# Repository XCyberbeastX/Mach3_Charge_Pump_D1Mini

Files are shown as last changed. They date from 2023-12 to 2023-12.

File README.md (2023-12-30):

# Mach3_Charge_Pump_D1Mini(ESP8266)

## Note:
This project is based on this [YouTube video](https://www.youtube.com/watch?v=voYk2AVyjqQ). Please be aware that I am not a professional circuit board designer and this information is shared from a hobbyist's perspective. Implementing this project is at your own risk, and it's advised to consult with a professional if needed.

## Info:
The charge pump circuit prevents the spindle from unintentionally starting while not using Mach3 with a parallel port. Especially during power up or down of the pc, this can lead to the parallel port outputs being switched randomly, posing a safety risk. The circuit, reads the 25/12,5 Khz signal of Mach3 and enables/disables the machine via a relay.

The Webinterface of the D1Mini (ESP8266) provides a easy way to read the charge pump frequency and relay state and can be further extended as needed.

The D1 Mini can be flashed using OTA through the 'ip/update' page after the first inital flash.

## 

*Make sure to enable the charge pump feature in Mach3 and assign a free pin.*

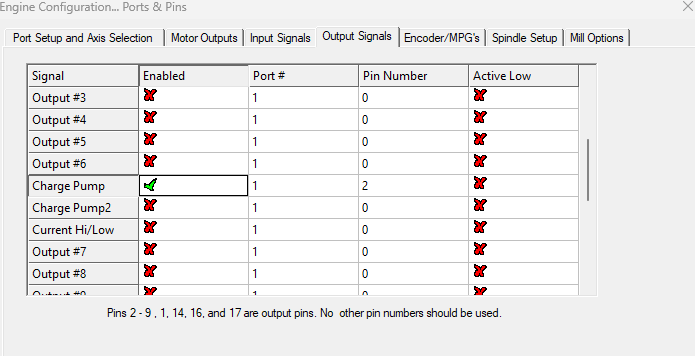
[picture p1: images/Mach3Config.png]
Mach3 Config


## Screenshots

*Website image*

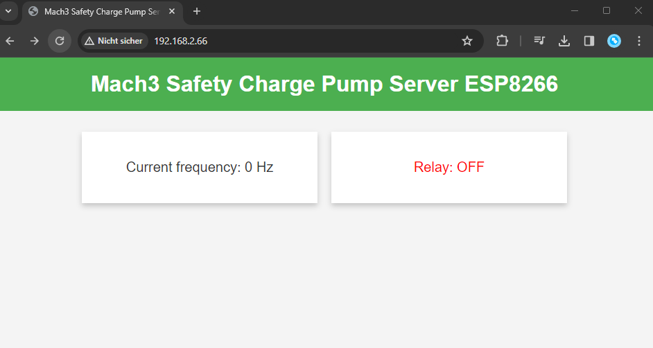
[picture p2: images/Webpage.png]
Webpage


*finished PCB for THT-Soldering, with bigger pads*

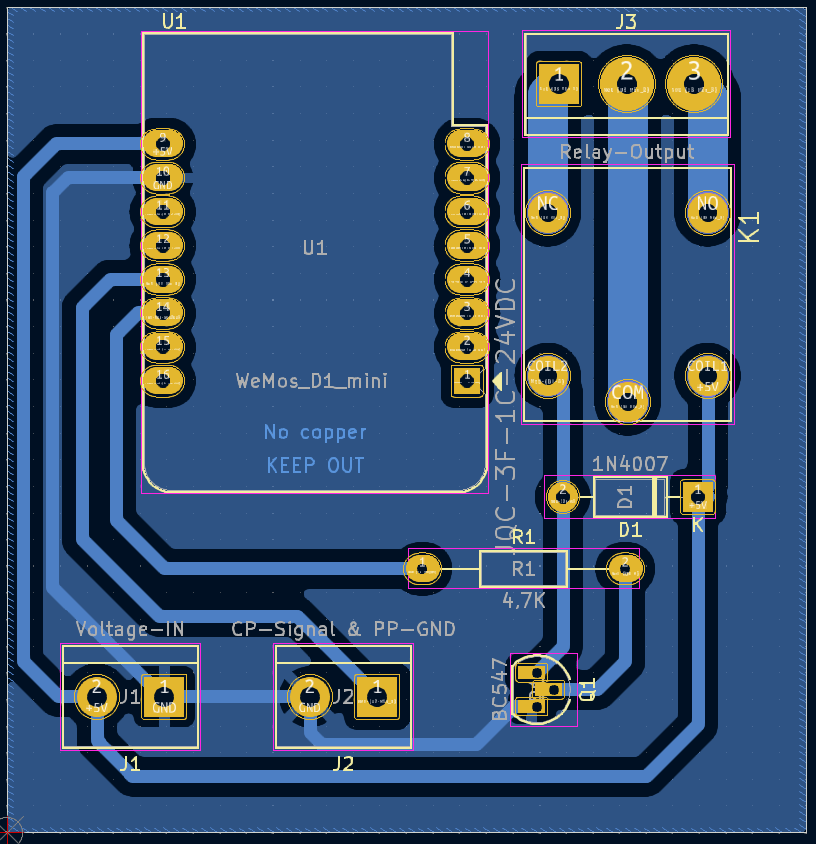
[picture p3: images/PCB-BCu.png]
PCB


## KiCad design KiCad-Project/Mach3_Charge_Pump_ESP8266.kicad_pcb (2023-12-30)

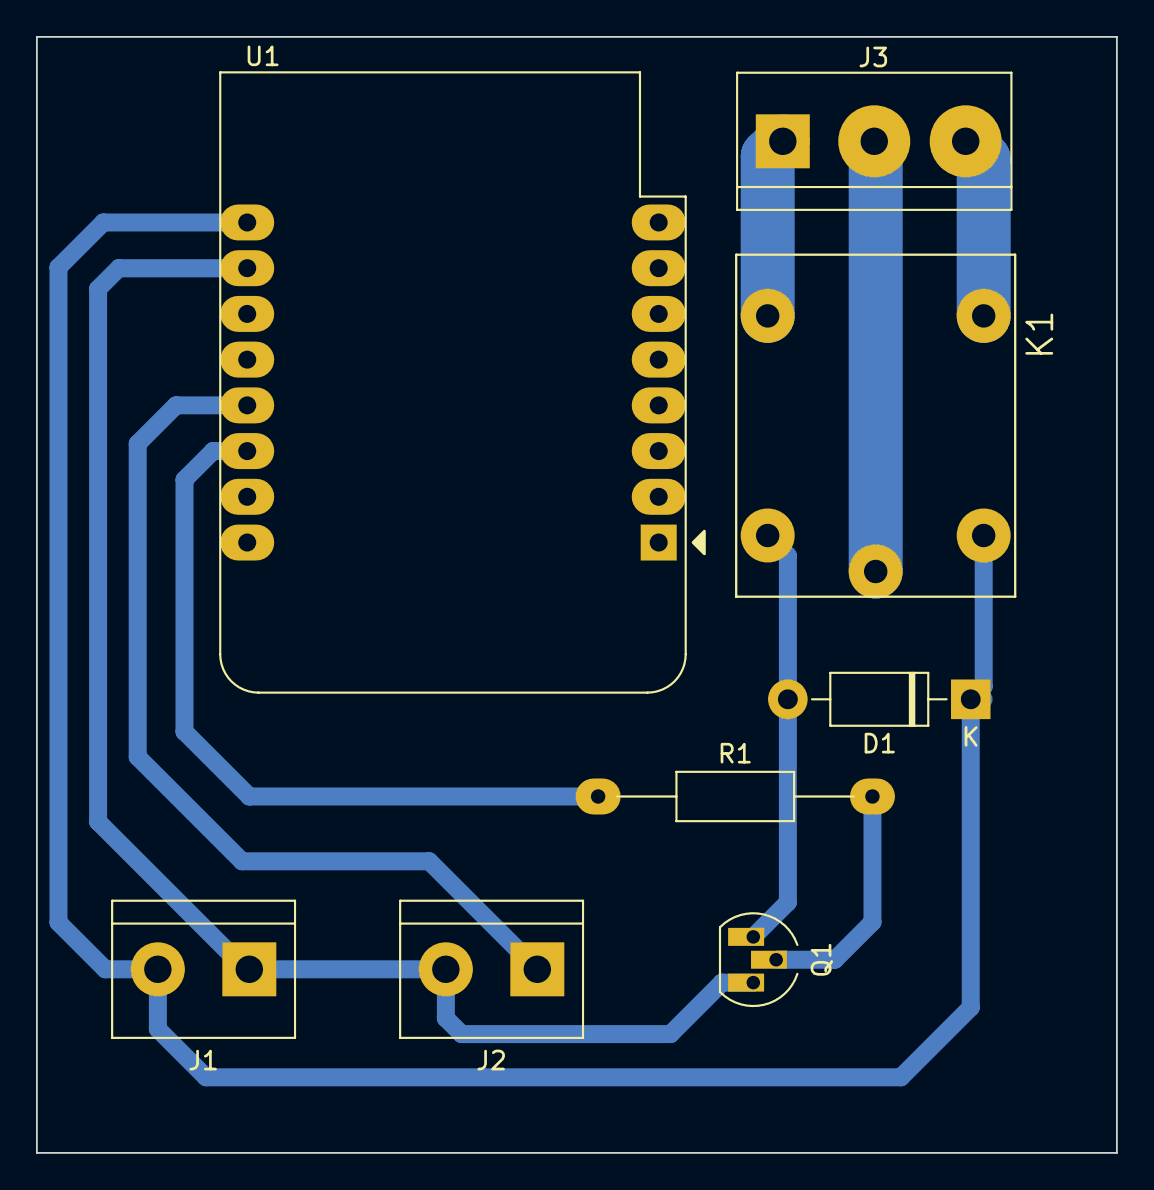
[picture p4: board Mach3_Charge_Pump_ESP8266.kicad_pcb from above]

Board: 2 copper layers, 60.0 x 62.0 mm, 8 parts (0 on the bottom side), 9 nets.

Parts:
D1: 1N4007; D_DO-41_SOD81_P10.16mm_Horizontal
J1: Voltage-IN; TerminalBlock_bornier-2_P5.08mm
J2: CP-Signal & PP-GND; TerminalBlock_bornier-2_P5.08mm
J3: Relay-Output; TerminalBlock_bornier-3_P5.08mm
K1: JQC-3F-1C-24VDC; RELAY_JQC-3F-1C-24VDC
Q1: BC547; TO-92L_HandSolder
R1: 4,7K; R_Axial_DIN0207_L6.3mm_D2.5mm_P15.24mm_Horizontal
U1: WeMos_D1_mini; WEMOS_D1_mini_light

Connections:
+5V: D1.1 (K), J1.2, K1.COIL1, U1.9 (5V)
GND: J1.1, J2.2, Q1.3 (E), U1.10 (GND)
unnamed: D1.2 (A), K1.COIL2, Q1.1 (C)
unnamed: J2.1, U1.13 (SDA/D2)
unnamed: J3.1, K1.NC
unnamed: J3.2, K1.COM
unnamed: J3.3, K1.NO
unnamed: Q1.2 (B), R1.2
unnamed: R1.1, U1.14 (SCL/D1)

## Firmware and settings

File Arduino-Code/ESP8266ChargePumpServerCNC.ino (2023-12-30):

#include <ESP8266WiFi.h>
#include <ESPAsyncTCP.h>
#include <ESPAsyncWebServer.h>
#include <AsyncElegantOTA.h>

enum RelayState
{
  ON,
  OFF
};

AsyncWebServer server(80);
const char *ssid = "CHANGE ME";
const char *password = "CHANGE ME";

// Change values according to your needs.
const byte MEASURE_PIN = 4;
const byte RELAY_PIN = 5;
const int THRESHOLD_FREQ = 25000;
const int MAX_DEVIATION = 5000;
const int MIN_REPS = 2;
const int TIMEOUT = 250;

RelayState currentRelayState = RelayState::OFF;
int reps = 0;
long currentFreq = 0;

void setup()
{
  Serial.begin(115200);
  WiFi.begin(ssid, password);

  pinMode(MEASURE_PIN, INPUT);
  pinMode(RELAY_PIN, OUTPUT);
  // Change the relay state according to your needs.
  digitalWrite(RELAY_PIN, LOW);
  currentRelayState = RelayState::OFF;

  while (WiFi.status() != WL_CONNECTED)
  {
    delay(500);
    Serial.print(".");
  }

  Serial.println("");
  Serial.print("Connected with SSID: ");
  Serial.println(ssid);
  Serial.print("Device ip-address: ");
  Serial.println(WiFi.localIP());

  server.on("/", HTTP_GET, [](AsyncWebServerRequest *request)
  {
    String html = "<!DOCTYPE html><html><head><title>Mach3 Safety Charge Pump Server ESP8266</title>";
    html += "<meta http-equiv='refresh' content='1'>";   //refresh page after every 1 sec
    html += "<meta name='viewport' content='width=device-width, initial-scale=1.0'>";
    html += "<style>";
    html += "body { font-family: 'Arial', sans-serif; margin: 0; padding: 0; background-color: #f4f4f4; color: #333; }";
    html += "h1 { background-color: #4CAF50; color: white; text-align: center; padding: 20px 0; margin: 0; }";
    html += ".container { padding: 20px; display: flex; justify-content: center; flex-wrap: wrap; }";
    html += ".card { background-color: white; box-shadow: 0 4px 8px 0 rgba(0,0,0,0.2); margin: 10px; padding: 20px; flex-basis: 300px; }";
    html += ".sensor, .relay { font-size: 20px; text-align: center; }";
    html += ".relay { color: " + String(currentRelayState == RelayState::ON ? "green" : "red") + "; }";
    html += "</style></head><body>";
    html += "<h1>Mach3 Safety Charge Pump Server ESP8266</h1>";
    html += "<div class='container'>";
    html += "<div class='card'><p class='sensor'>Current frequency: " + String(currentFreq) + " Hz</p></div>";
    html += "<div class='card'><p class='relay'>Relay: " +  String(currentRelayState == RelayState::ON ? "ON" : "OFF") + "</p></div>";
    html += "</div></body></html>";
    request->send(200, "text/html", html); 
  });

  AsyncElegantOTA.begin(&server);
  server.begin();
  Serial.println("Server started");
}

void loop()
{
  AsyncElegantOTA.loop();
  currentFreq = getFrequency(MEASURE_PIN);

  if (currentFreq > (THRESHOLD_FREQ - MAX_DEVIATION) && currentFreq < (THRESHOLD_FREQ + MAX_DEVIATION))
  {
    reps++;
    if (reps >= MIN_REPS)
    {
      // Change the relay state according to your needs.
      digitalWrite(RELAY_PIN, HIGH);
      currentRelayState = RelayState::ON;
    }
  }
  else
  {
    reps = 0;
    // Change the relay state according to your needs.
    digitalWrite(RELAY_PIN, LOW);
    currentRelayState = RelayState::OFF;
  }
}

long getFrequency(int pin)
{
  // reduce the number of samples for faster frequency read if needed
  int samples = 4096;
  long totalPulseTime = 0;
  long pulseTime;
  int validSamples = 0;

  for (int j = 0; j < samples; j++)
  {
    pulseTime = pulseIn(pin, HIGH, TIMEOUT);
    if (pulseTime > 0)
    {
      totalPulseTime += pulseTime;
      validSamples++;
    }
  }

  if (validSamples == 0)
  {
    return 0;
  }

  long averagePulseTime = totalPulseTime / validSamples;
  long frequency = 1000000L / averagePulseTime;
  return frequency;
}

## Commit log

2023-12-28 Added D1Mini Arduino code and image for readme
2023-12-30 Added KiCad Project + restructured repo
    [Mach3_Charge_Pump_ESP8266.kicad_pcb, Mach3_Charge_Pump_ESP8266.kicad_sch]
